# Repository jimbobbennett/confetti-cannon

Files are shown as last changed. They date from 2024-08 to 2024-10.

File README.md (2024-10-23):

# Confetti Cannon

This repo has all the materials for the Confetti Cannon demo for using Pieces.

An animated gif of the confetti cannon firing confetti across a conference

The confetti cannon is built around a Raspberry Pi with a 3D printed case, a motor, and spring-loaded confetti launchers. It is controlled by [Viam](https://www.viam.com), and the confetti is launched by code run locally another device.

This project is designed to show the snippet saving features of Pieces, and uses saved snippets for the code to fire the confetti cannon. The aim is to use this at an event, where an attendee will download Pieces, import a shared snippet, run this, launch confetti and win a prize!

## Hardware

The hardware you need is:

- [A Raspberry Pi 4 or higher](https://www.raspberrypi.com)
- A GPIO motor. We use this one: [Bemonoc 25GA370 DC Encoder Metal Gearmotor 12V](https://amzn.to/3yUJwUk)
- A [L298N Motor Driver](https://amzn.to/3yVtv0m)
- A 12v power supply, such as the [SoulBay 12V 1A AC Adapter](https://amzn.to/3XhhwDR)
- Jumper wires
- [Spring-loaded confetti launchers](https://amzn.to/4dGrCnu)
- A selection of M2.5 and M3 nuts and bolts

### Wiring

Use these diagrams for reference for the different pin connections.

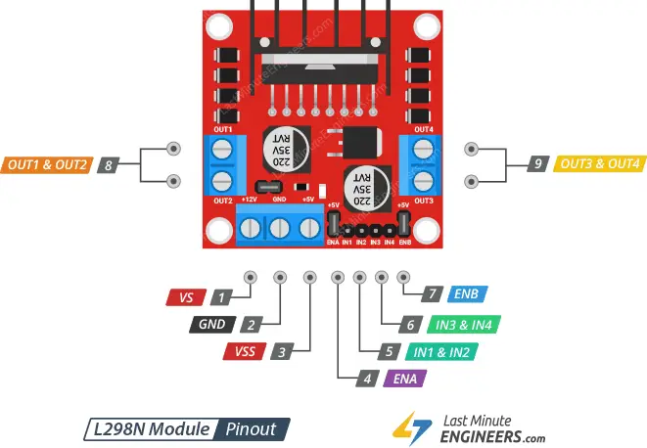
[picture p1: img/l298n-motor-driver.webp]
Pin diagram of the L298N motor driver

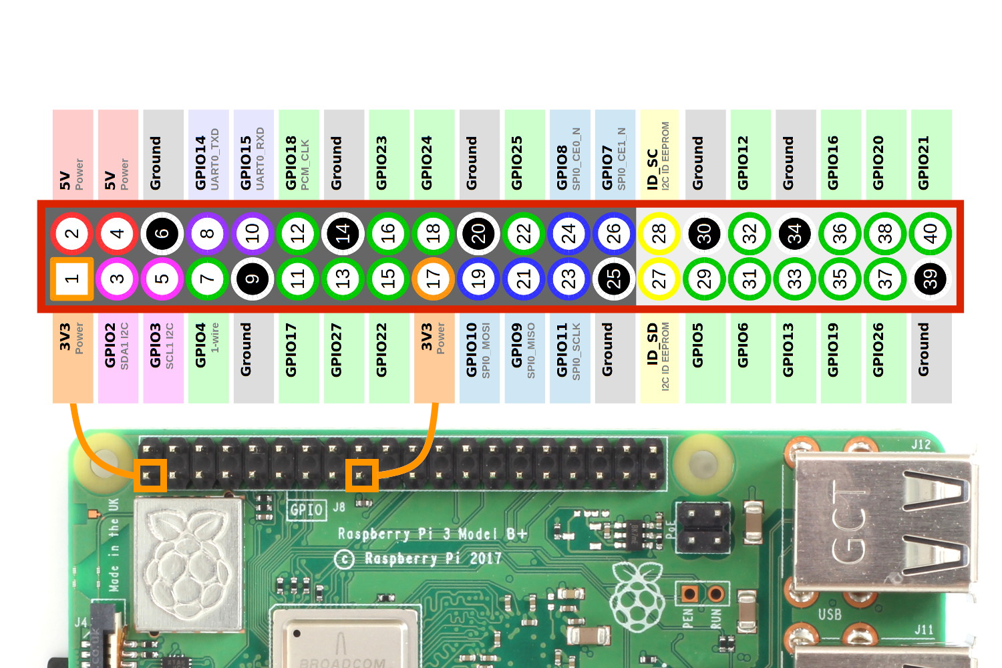
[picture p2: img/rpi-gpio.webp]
Raspberry Pi GPIO pins


Ensure both the 12v power supply and the Raspberry Pi are disconnected from power when wiring.

#### Power

1. Connect the __+ve__ terminal of the 12v supply to the __VS pin (pin 1)__ on the L298N motor driver.
1. Connect the __-ve__ terminal of the 12v supply to the __Gnd pin (pin 2)__ on the L298N motor driver.
1. Connect __pin 6__ on the Raspberry Pi (Ground) to the __Gnd pin (pin 2)__ on the L298N motor driver.

#### Motor control

1. Connect the __Out 1 pin__ (upper of the two 8 pins) on the L298N motor driver to the -ve connection on the motor. This is the __black__ wire from the connection block to the motor.
1. Connect the __Out 2 pin__ (lower of the two 8 pins) on the L298N motor driver to the +ve connection on the motor. This is the __red__ wire from the connection block to the motor.

#### L298N control

1. If there is a jumper connecting the __ENA pin__ (pin 4) on the L298N motor driver to  a __+5v pin__, remove it.
1. Connect the __ENA pin__ (pin 4) on the L298N motor driver to __pin 11__ (GPIO 17) on the Raspberry Pi.
1. Connect the __In1 & In2 pin__ (pin 5) on the L298N motor driver to __pin 13__ (GPIO 27) on the Raspberry Pi.
1. Connect the __In3 & In4 pin__ (pin 6) on the L298N motor driver to __pin 15__ (GPIO 22) on the Raspberry Pi.

## The case

The cannon is contained in a 3D printed case. You can find the STL files for this in the [`stl-files`](./stl-files/) folder.

| File | Description |
| --- | --- |
| main-frame.stl | The main case that holds the Raspberry Pi and motor driver |
| cannon-gripper.stl | A component that attaches the motor to the confetti launcher |
| cannon-guide.stl | A guide to hold the confetti launcher in place |
| cannon-offset.stl  | An offset to help put the guide in the right location |

### Assembly

1. Fix the motor through the hole in the main frame. You can fix it in place using a couple of M3 bolts through the frame into the holes in the motor.
1. Fit the cannon gripper to the shaft of the motor, and bolt in place using a metal bolt.
1. Attach the cannon offset to the main frame using M2 bolts and nuts.
1. Attach the cannon guide to the offset using M2 bolts and nuts.

## Software

For this project, you will need:

- A Viam project set up and configured with your hardware
- The Viam server installed on your Raspberry Pi
- Local code to control the Pi

### Set up the Pi

For the Raspberry Pi, you can use Raspberry Pi OS full or Lite. I recommend Lite as it is lighter weight and you don't need the desktop running.

1. Set up Raspberry Pi OS Lite (64-bit) on your [SD card as normal](https://www.raspberrypi.com/software/). Make sure you have SSH access to the Pi configured in the Raspberry Pi installer configuration.
1. Put the SD card into the Pi, power it up, and connect over SSH.
1. Update the Pi software:

    ```bash
    sudo apt update && sudo apt full-upgrade --yes && sudo reboot
    ```

1. The Pi will reboot once done, so reconnect.

### Set up Viam

1. Create an account with [Viam](https://viam.com) and ensure you are logged in. You can use the free version for this project.
1. In the [Viam app](https://app.viam.com), create  a new machine and name it `ConfettiCannon`.

    The new machine screen

1. The empty machine will be created, and there will be a __View setup instructions__ button. Select this button to see the setup instructions.
1. Set the _Platform_ to `Linux /Aarch 64`, and the _Installation method_ to `viam-agent`.
1. A set of installation instructions will be provided with a command to run on the Pi. Run this command on the Pi.

    The command will look something like this, but will have your API Key ID, Key and part ID.

    ```bash
    sudo /bin/sh -c "VIAM_API_KEY_ID=<key id> VIAM_API_KEY=<key> VIAM_PART_ID=<part id>; \
      $(curl -fsSL https://storage.googleapis.com/packages.viam.com/apps/viam-agent/install.sh)"
    ```

1. Once run, the Pi will be configured and will run the Viam agent automatically, even after a reboot. The setup option will disappear from the machine page, and be replaced with an empty machine.
1. Select the __+__ next to the machine name in the side bar, then select _Component->board->pi_ if you are using a Raspberry Pi 4, or _Component->board->pi5_ if you are using a Raspberry Pi 5. Name the board `cannon-controller`
1. Select the __+__ next to the machine name in the side bar, then select _Component->motor->gpio_ to add the motor. Name it `motor`.
1. In the `motor` section set the following:

    1. Set the _board_ to `cannon-controller`
    1. Expand the _Show more_ section and set the _max_rpm_ to `1000`.
    1. Set the _Component pin assignment_ to `In1/In2`. This refers to the connection on the motor driver.
    1. Set _a_ to `13`, _b_ to `15`, and _pwm_ to `11`. These are the positional values for the GPIO pins used on the Raspberry Pi. These are the positional numbers, not the GPIO pin numbers (for example, referring to the diagram above, the pin in position 11 is GPIO 27, so we set _pwm_ to 11).
1. Save the changes using the __Save__ button. The configuration will look like this:

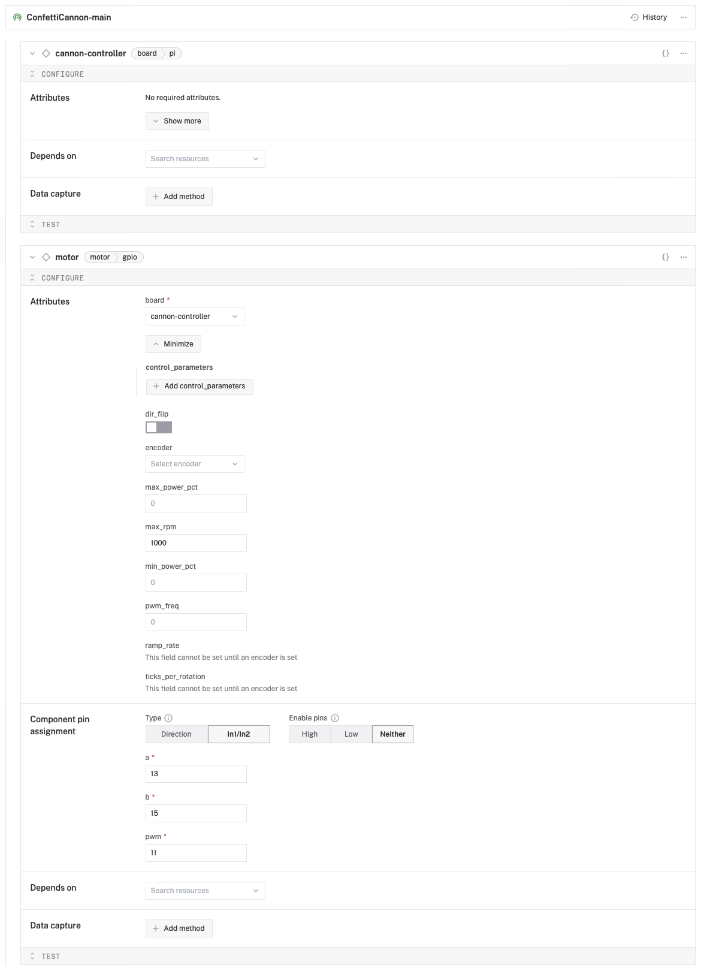
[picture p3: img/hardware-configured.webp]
The fully configured hardware
    

1. To test the motor, expand the _Test_ section in the `motor` block, and use the __Forward__ and __Backward__ buttons to spin the motor.
1. Slide a confetti popper into the gripper and guide, tightening the gripper in place to hold it.
1. Use the forward and backward buttons to launch the confetti!

## Control the Confetti Cannon

You can control the confetti cannon using code run from anywhere - the cannon is connected to Viam over the internet, so can be controlled from any internet connected device.

### Python

This repo contains a [`python`](./python/) folder with Python code to connect to Viam and launch the confetti cannon. To run this code, you will need to:

1. Set up a virtual environment and install the required Pip packages from the [`requirements.txt`](./python/requirements.txt) file.
1. Copy the [`.env.example`](./python/.env.example) file to `.env`, and fill in the values from your Viam project.
1. Run the code from the [`app.py](./python/app.py) file.

### Via a web server

If you want to run this code from an environment that doesn't support the Viam libraries, such as we did a FlutterCon, you can use a Python web server that runs on the device, and connect to this.

This code is in the [`app-server`](./app-server/) folder.

1. Set up a virtual environment and install the required Pip packages from the [`requirements.txt`](./app-server/requirements.txt) file.
1. Copy the [`.env.example`](./app-server/.env.example) file to `.env`, and fill in the values from your Viam project.
1. Run the [`main.py`](./app-server/main.py) file.

This will start an app server you can connect to. You can run this anywhere, including on the confetti cannon itself. I recommend using something like [ngrok](https://ngrok.com) to expose a tunnel so you can access this over the web.

You can then call this web server from anywhere.

- Make a `GET` request to `/` to get a status message to show the cannon is running
- Make a `POST` request to `/fire_cannon` passing the query string `key=pieces-confetti` to fire the cannon. The key is to allow you to share the code publicly without worrying about folks firing it without you being in control.

You can find an example `main.dart` for a Flutter app to launch the cannon in the [`flutter`](./flutter/) folder.

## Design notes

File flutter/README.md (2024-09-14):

# Confetti cannon Flutter code

This code can be added to a Flutter app to give a simple app with one button that fires the confetti cannon. You will need to have the [`app-server`](../app-server/) running, as this uses that to connect.

The aim of this code is to be shared as a Pieces snippet, so folks can add it to a new flutter app.

This is the description for the code snippet:

This code sample can be used to launch the Pieces confetti cannon at FlutterCon!

To use this:
1. Install Pieces, including the extension for your preferred IDE and your browser
2. Save this code snippet to Pieces
3. Create a new flutter app
4. Add the HTTP package:

    `flutter pub add http`

5. Replace the code in `main.dart` with this code snippet
6. Ask the Pieces team for the key, and update `key` with the value
7. Ask the Pieces team to prime a new confetti launcher
8. Run the Flutter app and press the Confetti button!

This has been tested with Chrome, iOS, Android and macOS.

For macOS, you will need to add:

<key>com.apple.security.network.client</key>
    <true/>

to your `macos/Runner/DebugProfile.entitlements` and `macos/Runner/ReleaseProfile.entitlements` files.

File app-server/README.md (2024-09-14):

# App server

This contains server code to run the confetti cannon. It can be used in situations where the VIAM SDK is not available, such as through Flutter (the VIAM flutter SDK is not currently working on any platform except iOS).

Run this as a web app, then share the port over the internet using [ngrok](https://ngrok.com) or [Local tunnel](https://theboroer.github.io/localtunnel-www/).

You will need to copy the `.env.example` file to `.env` and set the relevant values.

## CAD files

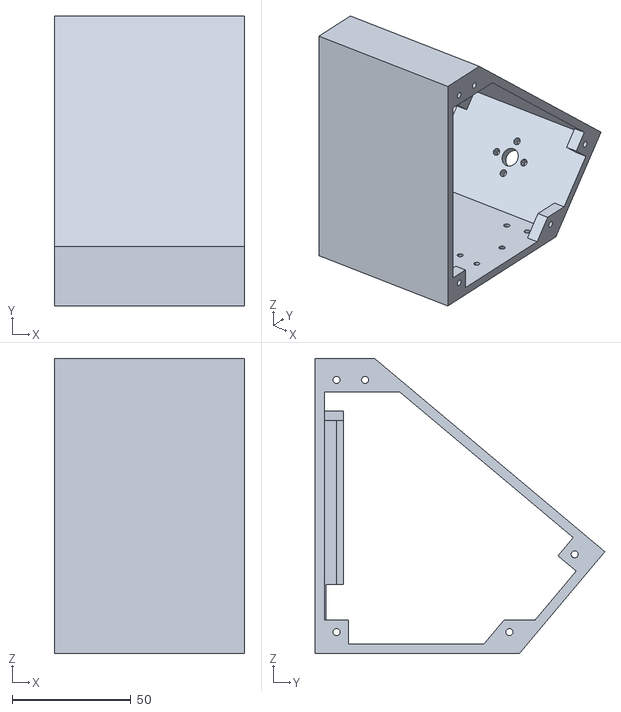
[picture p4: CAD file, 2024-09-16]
stl-files/main-frame.stl
80.0 x 121.8 x 124.0

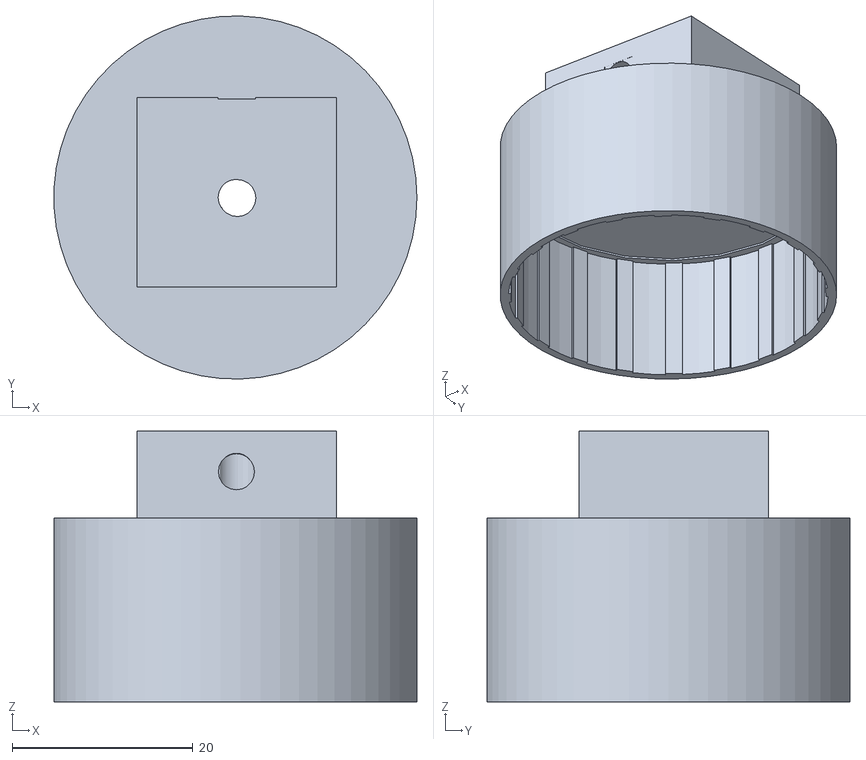
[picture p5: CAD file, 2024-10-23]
stl-files/cannon-gripper.stl
40.2 x 40.2 x 30.0

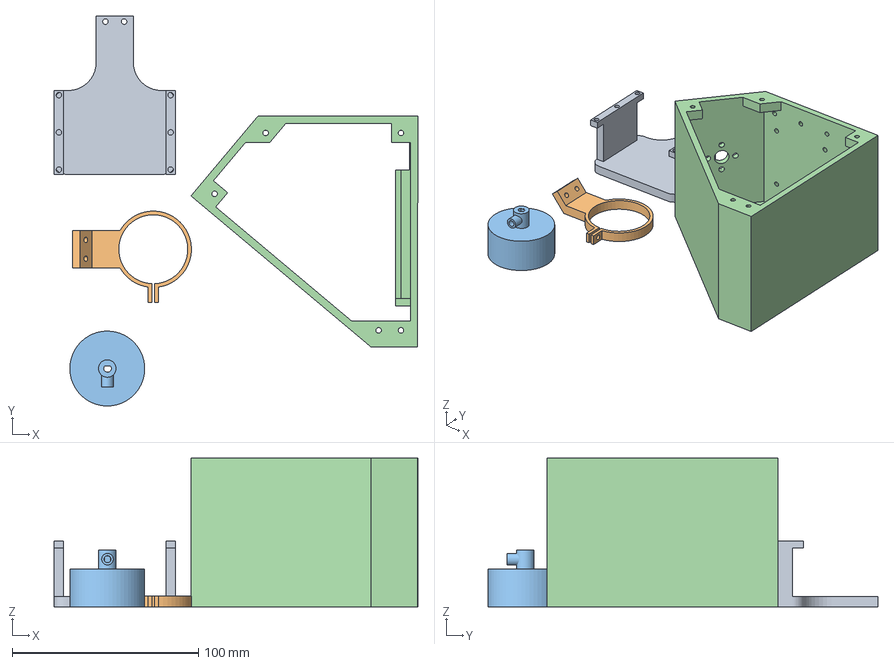
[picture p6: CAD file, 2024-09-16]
stl-files/cannon-bambu.3mf
195.2 x 209.4 x 80.0 mm
cyclyinder_offset.STL
confetti_latch.STL
Grand Densor-Bigery-2.stl
main-frame.stl

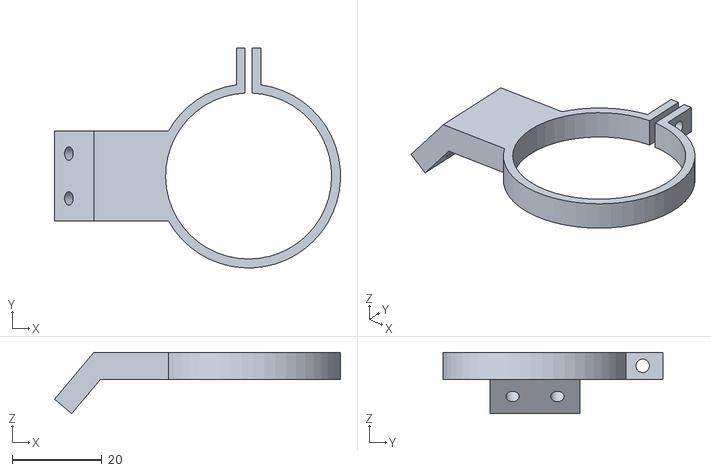
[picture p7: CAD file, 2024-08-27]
stl-files/cannon-guide.stl
63.7 x 49.0 x 13.7

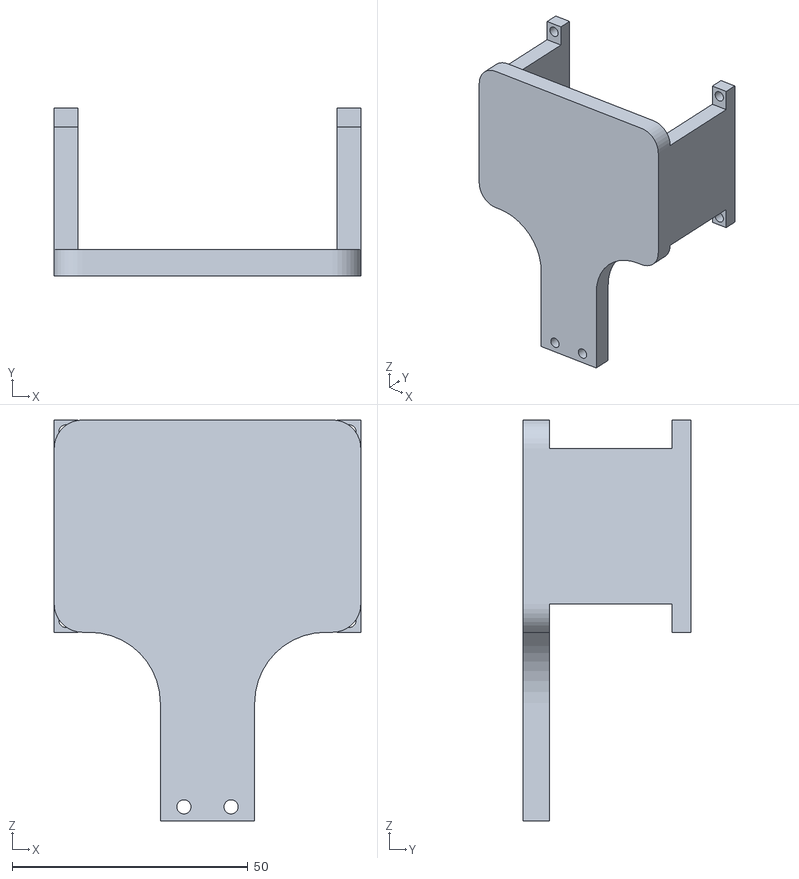
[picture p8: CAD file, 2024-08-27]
stl-files/cannon-offset.stl
65.0 x 35.6 x 85.0

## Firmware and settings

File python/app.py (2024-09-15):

"""
Robot Control Module

This module provides functionality to control a robot using the Viam SDK.
It establishes a connection to a remote robot, monitors a button press
on a GPIO pin, and controls a motor based on the button state.

The module uses environment variables for authentication and connection details:
- ROBOT_API_KEY: The API key for authenticating with the robot
- ROBOT_API_KEY_ID: The ID of the API key
- ROBOT_ADDRESS: The address of the robot (defaults to a specific cloud address if not provided)
"""
import asyncio
import os
from dotenv import load_dotenv

from viam.robot.client import RobotClient
from viam.components.motor import Motor

# Load the environment variables from the .env file
load_dotenv()

robot_api_key = os.getenv("ROBOT_API_KEY")
robot_api_key_id = os.getenv("ROBOT_API_KEY_ID")
robot_address = os.getenv("ROBOT_ADDRESS")


async def connect() -> RobotClient:
    """
    Establishes a connection to the robot client.

    This function creates a RobotClient instance using the provided API credentials
    and connects to a specific robot address.

    Returns:
        RobotClient: An instance of the RobotClient connected to the specified robot.

    Raises:
        Potential exceptions from RobotClient.at_address() if connection fails.
    """
    print(f"Connecting to robot {robot_address}")
    # Create options for the RobotClient using API key authentication
    options = RobotClient.Options.with_api_key(api_key=robot_api_key, api_key_id=robot_api_key_id)

    # Connect to the robot at the specified address using the created options
    return await RobotClient.at_address(robot_address, options)


async def main():
    """
    Main asynchronous function to control a robot based on button presses.
    """
    robot = await connect()
    print("Connected!")

    # Initialize the 'start' motor from the robot
    start: Motor = Motor.from_robot(robot, "motor")
    await start.set_rpm(150)

    # Spin the motor for 1 second

    try:
        # Set the motor power to 100%
        await start.set_power(1)

        # Small delay to prevent rapid toggling
        await asyncio.sleep(3)
    except:
        pass

    # Stop the motor
    await start.set_power(0)


if __name__ == "__main__":
    asyncio.run(main())

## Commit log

2024-08-27 First draft - needs 3D print assembly and final code
    [cannon-gripper.stl, cannon-guide.stl, cannon-offset.stl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]
2024-09-14 Samples for the confetti cannon
2024-09-15 Updating STL files
    [cannon-bambu.3mf, cannon-gripper.stl]
2024-09-16 Fixing models
    [cannon-bambu.3mf, main-frame.stl]
2024-09-16 Fixing motor spin time
